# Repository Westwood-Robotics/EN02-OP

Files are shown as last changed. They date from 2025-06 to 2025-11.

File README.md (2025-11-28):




# EN02-OP

EN02-OP is the Open Source 3-Finger End-Effector created by Westwood Robotics and equiped on our full-size humanoid robot THEMIS. A very simple yet versital 7DoF design is adopter, enabling the end-effector to change into the best poses for all kinds of items. \
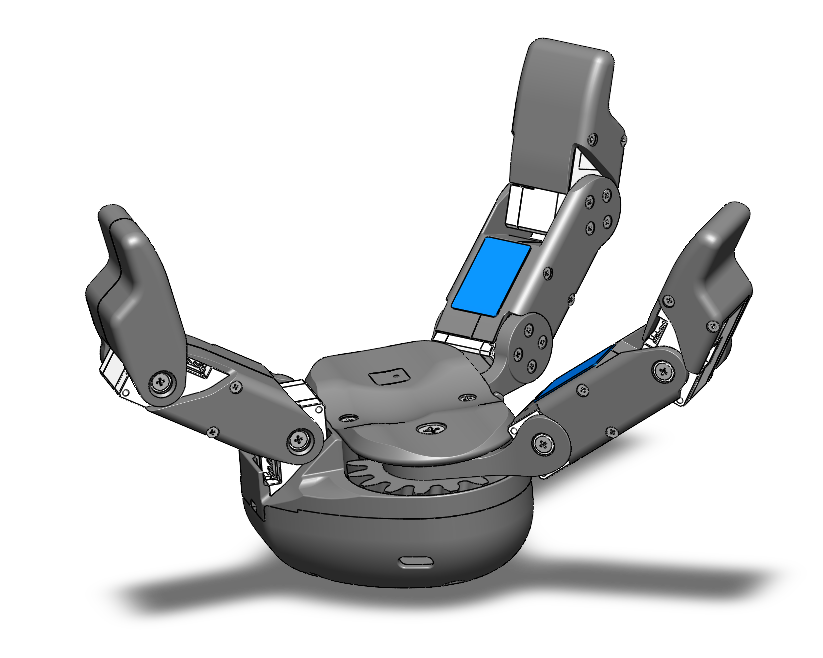
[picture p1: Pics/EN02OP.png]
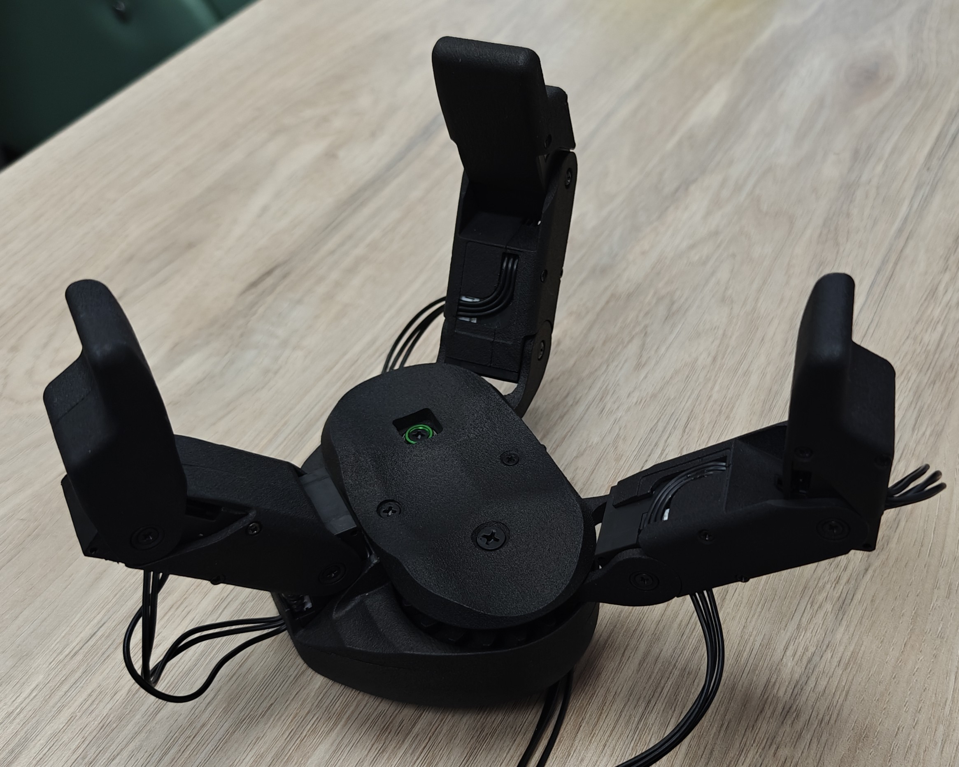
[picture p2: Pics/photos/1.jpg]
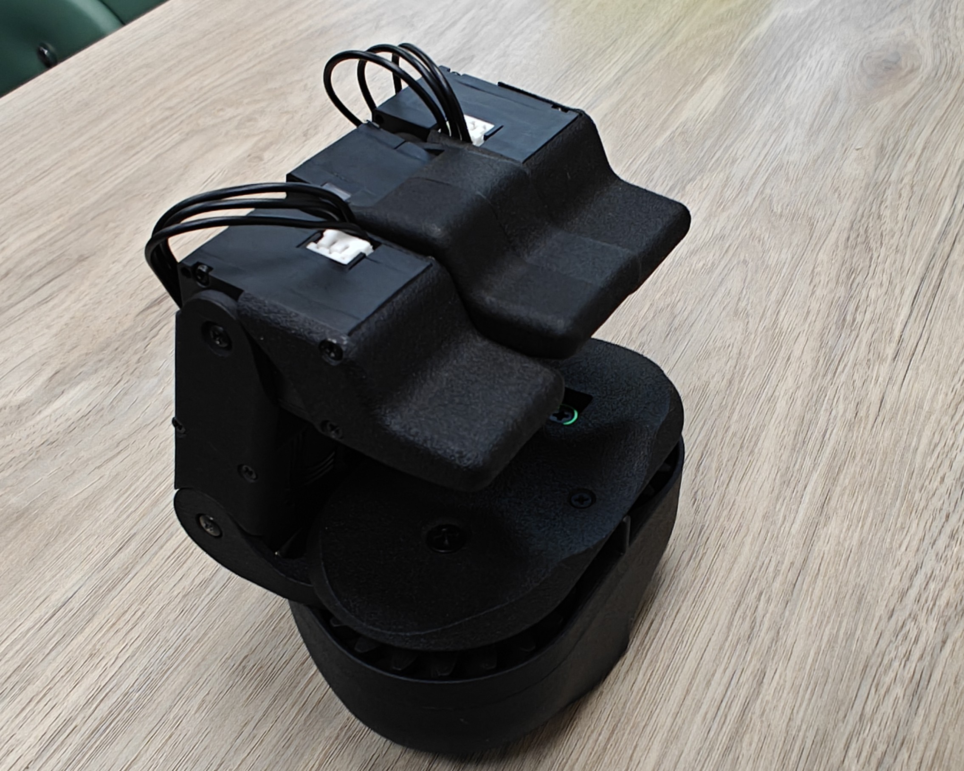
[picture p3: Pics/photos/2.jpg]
  \
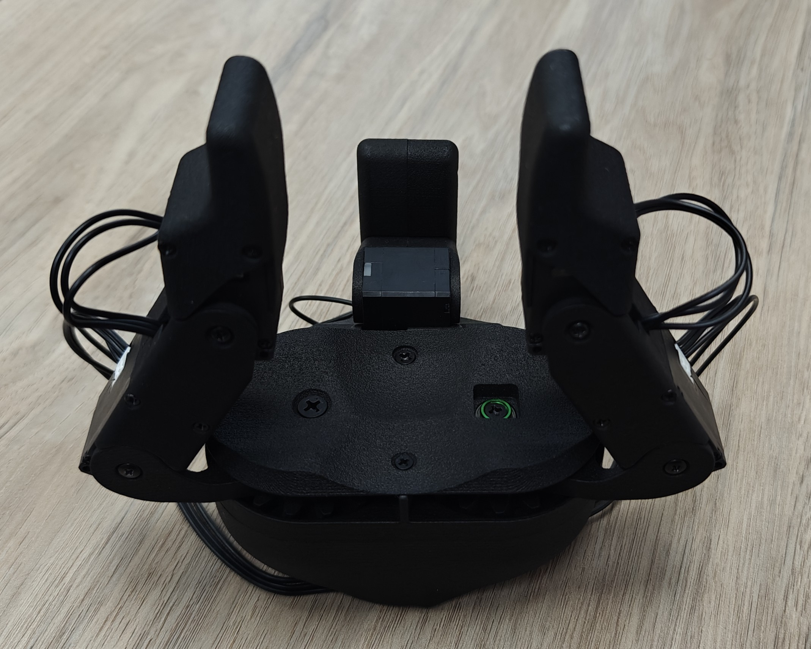
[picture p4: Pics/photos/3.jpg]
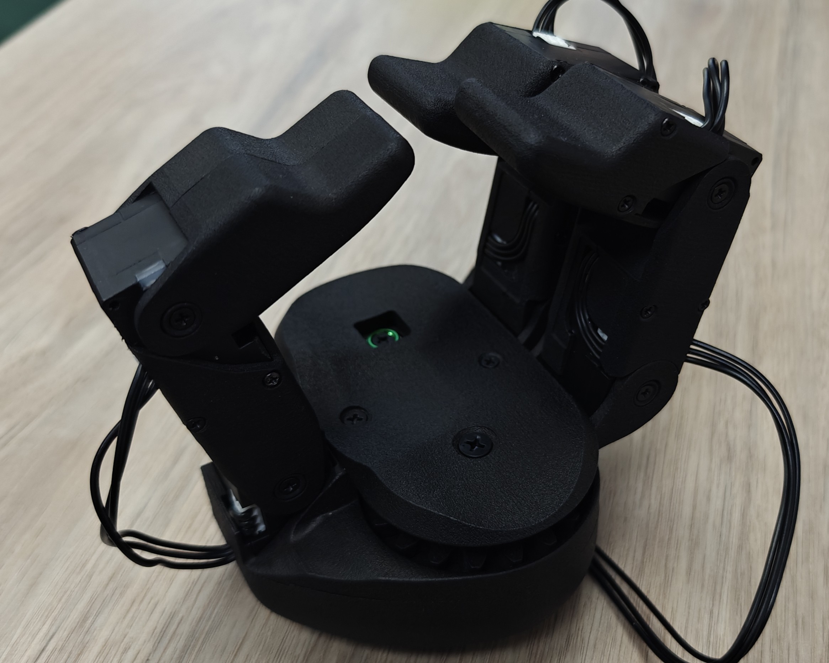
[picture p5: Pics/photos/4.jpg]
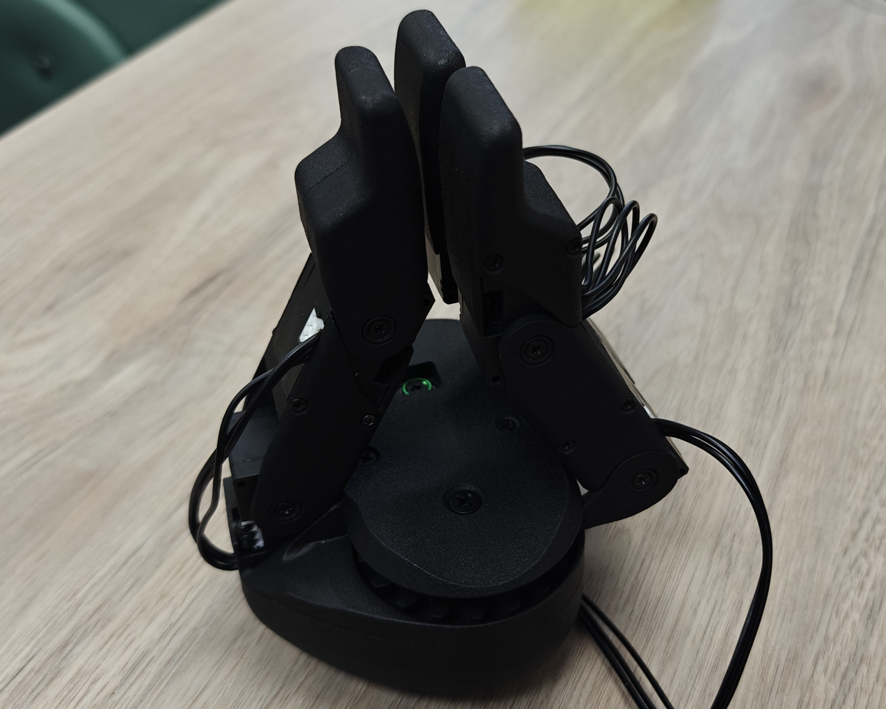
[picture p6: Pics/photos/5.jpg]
  \
Most parts on EN02-OP can be 3D printed, and all hadrware is standard and avalible off-the-shelf. The standard actuators on EN02-OP are the XC-330-M288-T($98.89/ea) from Dynamixel, but if the anticipated payload is realtively small, XL-330($26.29/ea) can be adopted for lower cost.

[Contact us](https://www.westwoodrobotics.io/contact/) to order an official version, or ***Build your EN02-OP for as low as $200!*** \
<sub> (Cost estimation based on using XL-330 for all 7DoF, parts printed with generic PLA material and Bambu PAHT-CF, and EN02OP-PWR PCBA assembled in-house. Tools and equipment not included.)  </sub>

## Build EN02-OP with Kevin!
Follow [this tutorial](https://www.youtube.com/watch?v=WY0bp_8Il1o) by [Kevin Wood](https://github.com/kevinwoodrobotics) to build your EN02-OP!

## Before You Start
### Know The Design
> [!IMPORTANT]
> Modify EN02-PALM_BASE to fit your system before printing.

> [!NOTE]
> Use fiber reinforced materials for parts in */Design/Parts_to_Print/CF_Reinforced/*

All design files of EN02-OP is included in [EN02-OP.STEP](/Design/EN02-OP.STEP). To make import easier, the 3D model of EN02OP-PWR(Board for voltage regulation and communication ports) is excluded from the model and provided seperatly in [EN02-PWR.step](/Design/EN02-PWR.step). Refer to [EN02-OP-BOM.xls](/Design/EN02-OP-BOM.xls) for the complete BOM of EN02-OP.

For your convenient, all parts that can be 3D printed are included in the [/Design/Parts_to_Print](/Design/Parts_to_Print/) folder. \
Feel free to go with your favorate materials for the parts in the [../Parts_to_Print/General](/Design/Parts_to_Print/General/) folder, such as PLA, PETG, ABS and Nylon, but it is highly recommended to print the parts in the [../Parts_to_Print/CF_Reinforced](/Design/Parts_to_Print/CF_Reinforced/) folder with carbon fiber/glass fiber reinforced materials for better strength and durability, such as Bambu PAHT-CF. The parts are highlighted in blue in the picture below:\
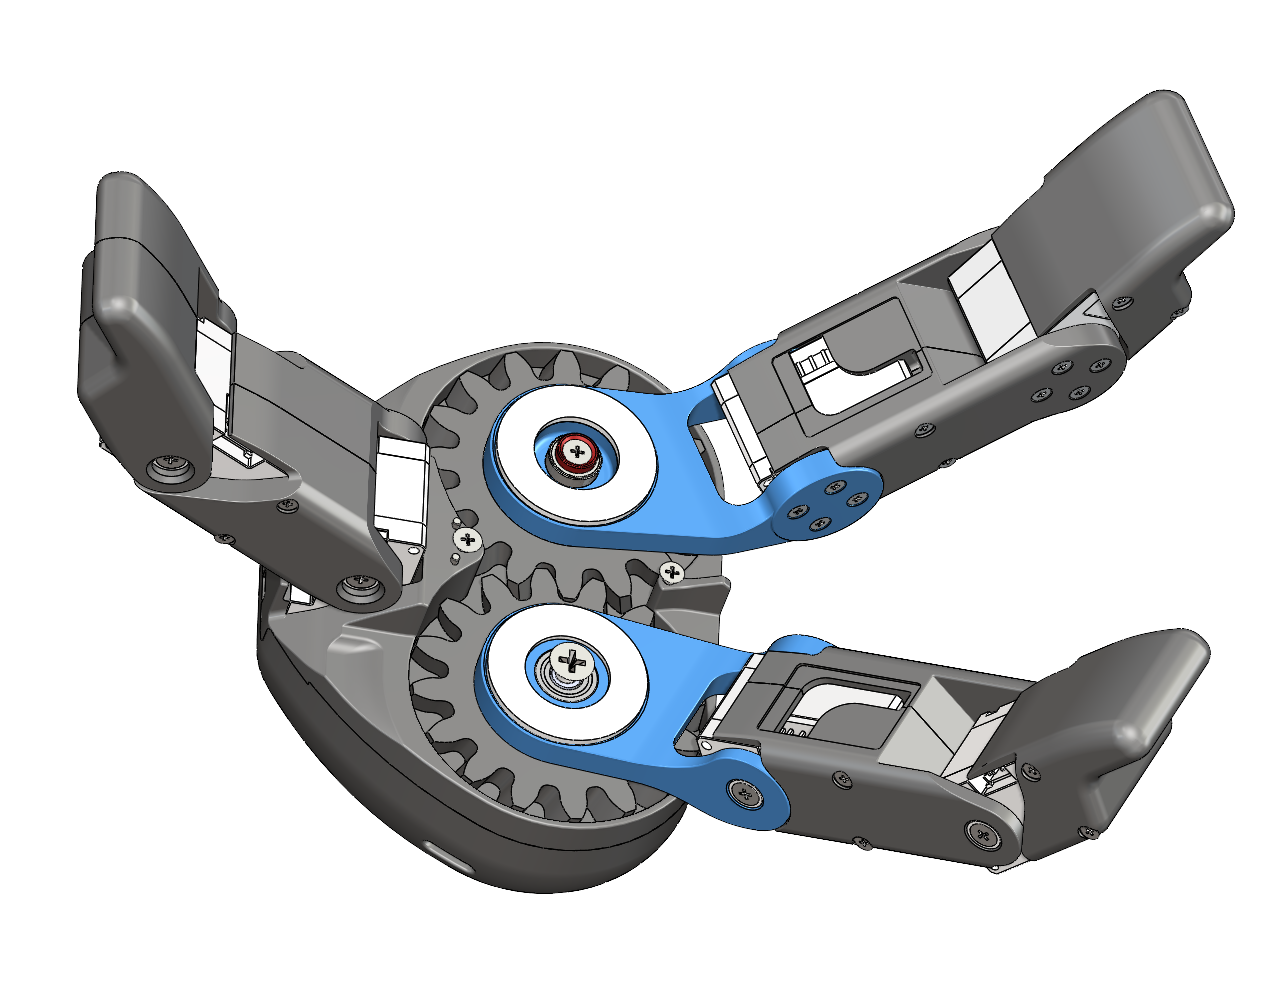
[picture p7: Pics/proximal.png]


**Modify [EN02-PALM_BASE](/Design/Parts_to_Print/General/Modify_Before_Printing/EN02-PALM_BASE.STEP) before printing!** \
EN02-OP is designed to be located and mounted onto robot manipulators using the plane with circular profile on the bottom, as highlighted in blue in the piture below. Mounting holes have been removed intentionally, so please modify the part and add mounting holes in a pattern that matches your robot manipulator before printing it.\
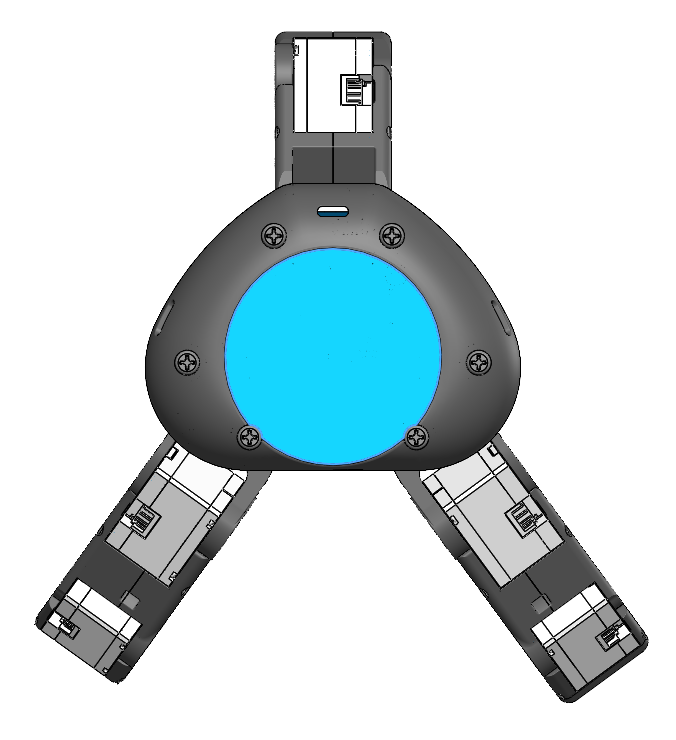
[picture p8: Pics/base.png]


### Electronics 
Electronics on EN02-OP is fairly simple and there is only one PCBA to fabracate which is the EN02-PWR. The XL/XC-330-M288-T actuators take 5V as input and their communication protocal is TTL. There is a 20~36V to 5V/10A regulator on EN02-PWR, making it compatible with the DC power supply on a large range of robot systems. It also takes care of chaining the fingers together. 

All related files are included in the [/Electronics](/Electronics) folder. Send [EN02OP-PWR-Gerber.zip](/Electronics/EN02OP-PWR-Gerber.zip) to your PCB manufacture to make the PCB board, and all components needed are listed in [EN02OP-PWR-BOM.xlsx](/Electronics/EN02OP-PWR-BOM.xlsx). Refer to [EN02OP-PWR.pdf](/Electronics/EN02OP-PWR.pdf) for the scheme of the board.

You can purchase pre-assembled EN02OP-PWR from us for $35/ea. Contact us at: https://www.westwoodrobotics.io/contact/

Each XL/XC-330 actuator comes with one pre-assembled cable. Cables with the same crimp and headers(JST EHR-03) in various length can also be found on Amazon and Ebay for affordable prices.
#### Can I modify EN02-PWR to support 12V systems?
Other models of XC330 actuators such as the T288 and the T181 models require 12V power supply, and EN02-PWR can be easily modified by relacing several components to support 12V. Please refer to tab "BOM_12V_EN02OP" in [EN02OP-PWR-BOM.xlsx](/Electronics/EN02OP-PWR-BOM.xlsx) for a full BOM for 12V output, and the items that are different from 5V setup has been highlighted.
> [!IMPORTANT]
> Make sure to always test the output of your EN02-PWR before using it. Avoid powering 5V actuators with 12V power supply.

> [!NOTE]
> The pre-assembled EN02OP-PWR from Westwood Robotics is 5V. You will need to modify the components according to BOM_12V_EN02OP by yourself if 12V is needed instead of 5V. Please note that any modification will void the board's warranty. 

## Assembly Notes
Please refer to [EN02 Assembly Guide.pdf](/EN02_Assembly_Guide.pdf) for detailed assemble instructions. Feel free to contact us should you encounter any challenge.

## Control Software
There is no dedicated control software for EN02-OP at the moment. It is realatively easy to work with given its simple structure, and please refer to https://emanual.robotis.com/docs/en/dxl/x/xc330-m288/ for more information on how to work with Dynamixel actuators.

## Licensing
The work in this repo is under GNU General Public License (GPL) version 3, which is ideal for use cases such as open-source projects with open-source distribution, student/academic purposes, hobby projects, internal research projects without external distribution, or other projects where all GPL obligations can be met. Read the full text of [the GNU GPL version 3](https://www.gnu.org/licenses/gpl-3.0.html) for details.  

Contact us for commercial license should you need full rights to create and distribute the platform on your own terms without any open-source license obligations.

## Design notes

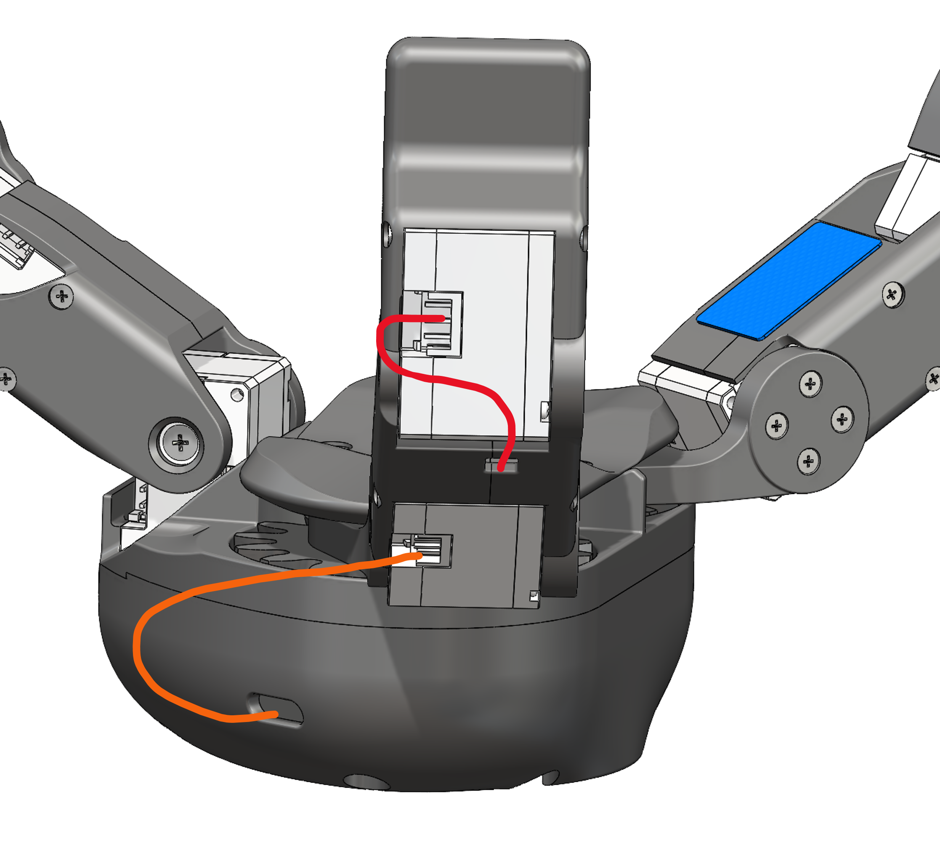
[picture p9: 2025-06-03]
Pics/wire2.png

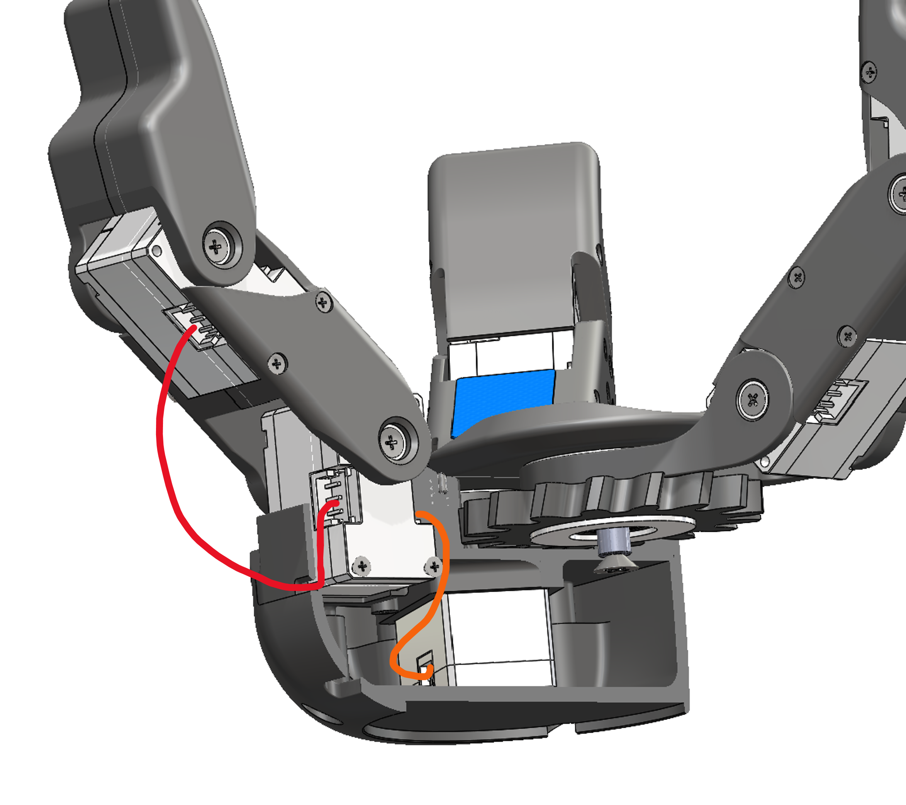
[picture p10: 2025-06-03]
Pics/wire3.png

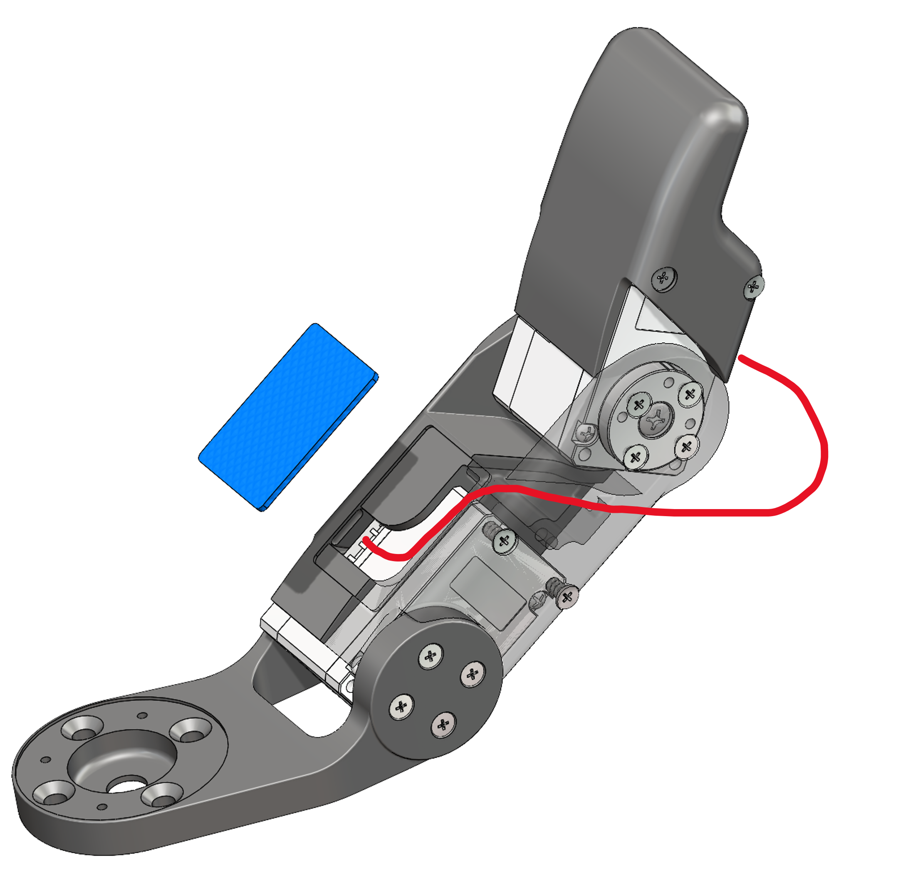
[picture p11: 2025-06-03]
Pics/wire1.png

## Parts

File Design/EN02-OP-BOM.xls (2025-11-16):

Item | Part# | Name | Description | QTY | Note
1 | EN02-01-01-01 | EN02-PALM_TOP |  | 1 | Print with PLA/ABS/Nylon/PETG
2 | EN02-01-01-02 | EN02-PALM_TOP_CAP |  | 1 | Print with PLA/ABS/Nylon/PETG
3 | EN02-01-01-03 | EN02-PALM_MIDHOUSING |  | 1 | Print with PLA/ABS/Nylon/PETG
4 | EN02-01-01-04 | EN02-PALM_BASE |  | 1 | MODIFY BEFORE PRINTING; Print with PLA/ABS/Nylon/PETG
5 | EN02-01-02-01 | EN02-MASTER_GEAR | M3_T16_H6_15deg_DC_-1.0 | 1 | Print with PLA/ABS/Nylon/PETG
6 | EN02-01-02-02 | EN02-SLAVE_GEAR | M3_T16_H6_15deg_DC_-1.0_SLAVE | 1 | Print with PLA/ABS/Nylon/PETG
7 | EN02-01-02-03 | EN02-SLAVE_SHAFT |  | 1 | Print with PLA/ABS/Nylon/PETG
8 | EN02-01-03-01 | EN02-PWR | EN02-POWER_BOARD, 5V OUTPUT, 20-36V INPUT | 1 | Solder power cable before assembly
9 | EN02-01-03-02 | EN02-DXL_CABLE_S | EHR cable for Dynamixel Actuators, 15~16cm | 3
10 | EN02-01-03-03 | EN02-DXL_CABLE_L | EHR cable for Dynamixel Actuators, 19~20cm | 3
11 | EN02-01-03-04 | EN02-DXL_CABLE_J | EHR cable for Dynamixel Actuators, 5~6cm | 1
12 | EN02-02-01-01 | EN02-PROXIMAL_PHALANX |  | 1 | Print with CF reinforced materials
13 | EN02-02-02-01 | EN02-MIDDLE_PHALANX |  | 1 | Print with PLA/ABS/Nylon/PETG
14 | EN02-02-03-01 | EN02-DISTAL_PHALANX |  | 1 | Print with PLA/ABS/Nylon/PETG
15 | EN02-03-01-01 | EN02-PROXIMAL_PHALANX-M |  | 1 | Print with CF reinforced materials
16 | EN02-03-02-01 | EN02-MIDDLE_PHALANX_M |  | 1 | Print with PLA/ABS/Nylon/PETG
17 | EN02-03-03-01 | EN02-DISTAL_PHALANX-M |  | 1 | Print with PLA/ABS/Nylon/PETG
18 | EN02-04-01-01 | EN02-THUMB_MIDDLE_PHALANX |  | 1 | Print with PLA/ABS/Nylon/PETG
19 | EN02-04-02-01 | EN02-THUMB_DISTAL_PHALANX |  | 1 | Print with PLA/ABS/Nylon/PETG
20 | XL-XC-330 | DYNAMIXEL XC/XL330-M288-T | DYNAMIXEL SERVO ACTUATOR | 7
21 | IDLER-XL-XC-330 | IDLER | IDLER FOR 330 ACTUATOR | 7 | Print with PLA/ABS/Nylon/PETG
22 | JTM-1630-015 | THRUST_BEARING_16x30x1.5 | IGUS Thrust Washer | 3
23 | 106ZZ | 106ZZ | Precision Stainless Steel Ball Bearing | 1
24 | 126ZZ | 126ZZ | Stainless Steel Ball Bearing | 2
25 | WASHER_M3_FLATHEAD | METAL WASHER FOR FLATHEAD SCREW, M3 | METAL WASHER FOR FLATHEAD SCREW, M3 | 1
26 | TRS-M3x8_FLAT | TRS-M3x8_FLAT | Stainless Steel Flat Head Thread-Forming Screws for Plastic | 7
27 | TRS-M2.2x12_FLAT | TRS-M2.2x12_FLAT | Stainless Steel Flat Head Thread-Forming Screws for Plastic | 28
28 | TRS-M2x5_FLAT_PHILLIPS | TRS-M2x5_FLAT_PHILLIPS | Stainless Steel Flat Head Thread-Forming Screws for Plastic | 24
29 | TRS-M2.5x24_FLAT_PHILLIPS | TRS-M2.5x24_FLAT_PHILLIPS | Stainless Steel Flat Head Thread-Forming Screws for Plastic | 2
30 | TRS-M3x12_FLAT | TRS-M3x12_FLAT | Stainless Steel Flat Head Thread-Forming Screws for Plastic | 1
31 | TRS-M3x10_FLAT | TRS-M3x10_FLAT | Stainless Steel Flat Head Thread-Forming Screws for Plastic | 8
32 | TRS-M2x8_FLAT_PHILLIPS | TRS-M2x8_FLAT_PHILLIPS | Stainless Steel Flat Head Thread-Forming Screws for Plastic | 4
33 | TRS-M2.5x8_FLAT | TRS-M2.5x8_FLAT | Stainless Steel Flat Head Thread-Forming Screws for Plastic | 1
34 | TRS-M4x10_ROUND | TRS-M4x10_ROUND | Phillips Rounded Head Thread-Forming Screws | 6
35 | TRS-M4x12_FLAT | TRS-M4x12_FLAT | Stainless Steel Flat Head Thread-Forming Screws for Plastic | 2
36 | TRS-M2.5x6_ROUND | TRS-M2.5x6_ROUND | Phillips Rounded Head Thread-Forming Screws | 1
37 | D1.5x5 | DOWEL PIN, DIAMETER 1.5MM, LENGTH 5MM | 18-8 Stainless Steel Dowel Pin | 2
38 | D1.5x10 | DOWEL PIN, DIAMETER 1.5MM, LENGTH 10MM | 18-8 Stainless Steel Dowel Pin | 6
39 | D2x5 | DOWEL PIN, DIAMETER 2MM, LENGTH 5MM | 18-8 Stainless Steel Dowel Pin | 5
40 | SW-4 | Spiral Wrap, ID 4mm

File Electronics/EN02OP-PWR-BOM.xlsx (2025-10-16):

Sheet: BOM_5V_EN02OP
No. | Quantity | Designator | Footprint | Value | Comment | Description
1 | 2 | C11,C12 | C1210 | 4.7uF | 4.7uF | Capacitance:4.7uF;Tolerance:±10%;Rated Voltage:100V;Capacitance:Temperature Coefficient:X7S;
2 | 1 | C13 | C0805 | 470nF | 470nF | Capacitance:470nF;Tolerance:±10%;Rated Voltage:100V;Capacitance:Temperature Coefficient:X7R;
3 | 1 | C15 | C0603 | 1uF | 1uF | Capacitance:1uF;Tolerance:±10%;Rated Voltage:16V;Capacitance:Temperature Coefficient:X7R;
4 | 1 | C16 | C0805 | 4.7uF | 4.7uF | Capacitance:4.7uF;Tolerance:±10%;Rated Voltage:16V;Capacitance:Temperature Coefficient:X7R;
5 | 1 | C18 | C0603 | 680pF | 680pF | Capacitance:680pF;Tolerance:±10%;Rated Voltage:50V;Capacitance:Temperature Coefficient:X7R;
6 | 1 | C20 | C0603 | 10nF | 10nF | Capacitance:10nF;Tolerance:±10%;Rated Voltage:50V;Capacitance:Temperature Coefficient:X7R;
7 | 1 | C21 | C0603 | 100nF | 100nF | Capacitance:100nF;Tolerance:±10%;Rated Voltage:16V;Capacitance:Temperature Coefficient:X7R;
8 | 1 | C23 | C1210 | 22uF | 22uF | Capacitance:22uF;Tolerance:±10%;Rated Voltage:16V;Capacitance:Temperature Coefficient:X7R;
9 | 1 | C24 | C0603 | 220pF | 220pF | Capacitance:220pF;Tolerance:±10%;Rated Voltage:100V;Capacitance:Temperature Coefficient:X7R;
10 | 1 | C26 | CAP-SMD_L7.3-W4.3-L-FD | 220uF | Tantalum Capacitors | Capacitance:220uF;Tolerance:±20%;Rated Voltage:16V
11 | 1 | C27 | C0603 | NS | NS
12 | 1 | C28 | C0603 | NS | NS
13 | 1 | CN1 | CONN-SMD_4P-P1.25-Horizontal
14 | 1 | D1 | SOD-323_L1.8-W1.3-LS2.5-RD |  | 1N4148WS | Switching Diodes, 1N4148WS
15 | 1 | D2 | POWERDI-123_L2.8-W1.8-LS3.7-RD |  | DFLS1150-7 | Schottky Diodes 150V 1A
16 | 3 | INDEX_L,INDEX_R,THUMB | CONN-TH_3P-P2.50-Horizontal |  | S3B-EH(LF)(SN)
17 | 1 | L2 | IND-SMD_L13.45-W12.6 | 4.7uH | 4.7uH | 4.7uH;Tolerance:±20%;Rated Current:15A;
18 | 2 | Q3,Q4 | DFN-8_L3.0-W3.0-P0.65-BL-EP_PE5G6EA |  | WSD4038DN33 | 40V 38A 2.1W 13mΩ@10V,7A 2.5V 1 N-channel DFN-8(3x3) MOSFETs
19 | 2 | R10,R16 | R0603 | 37.4kΩ | 37.4kΩ | Resistance:37.4kΩ;Tolerance:±1%;Power:100mW;Temperature Coefficient:±100ppm/℃;SMD
20 | 2 | R11,R13 | R0603 | 100kΩ | 100kΩ | Resistance:100kΩ;Tolerance:1%;Power:100mW;
21 | 5 | R12,R19,R21,R24,R25 | R0603 | 0Ω | 0Ω | Resistance:0Ω;Tolerance:±5%;Power:100mW;Temperature Coefficient:±800ppm/℃;SMD
22 | 1 | R14 | R0603 | 1MΩ | 1MΩ | Resistance:1MΩ;Tolerance:±1%;Power:100mW;Temperature Coefficient:±100ppm/℃;SMD
23 | 1 | R17 | R0603 | 51kΩ | 51kΩ | Thick Film Resistors
24 | 2 | R18,R30 | R0603 | NS | NS
25 | 1 | R20 | R0603 | 2.2Ω | 2.2Ω | Resistance:2.2Ω;Tolerance:±1%;Power:100mW;Temperature Coefficient:±400ppm/℃;SMD
26 | 2 | R22,R29 | R0603 | 10 | 10 | Resistance:10Ω;Tolerance:±1%;Power:100mW;Temperature Coefficient:±400ppm/℃;SMD
27 | 1 | R23 | RES-SMD_L6.4-W3.2-1 | 7mΩ | 7mΩ | Resistance:7mΩ;Tolerance:±1%;Power:2W;Temperature Coefficient:±100ppm/℃;
28 | 1 | R26 | R0603 | 63.4K | 63.4K | Thick Film Resistors
29 | 1 | R27 | R0603 | 12kΩ | 12kΩ | Resistance:12kΩ;Tolerance:±1%;Power:100mW;Temperature Coefficient:±100ppm/℃;SMD
30 | 1 | U5 | TSSOP-20-EP |  | MP9928GF | 4V-60V INPUT, CURRENT MODE, SYNC
31 | 1 | U13 | CAP-SMD_BD6.3-L6.6-W6.6-FD | 47uF | 47uF | 47uF 50V 195mA@100kHz 680mΩ@100kHz ±20% SMD,D6.3xL5.8mm Aluminum Electrolytic Capacitors

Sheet: BOM_12V_EN02OP
No. | Quantity | Designator | Footprint | Value | Comment | Description
1 | 2 | C11,C12 | C1210 | 4.7uF | 4.7uF | Capacitance:4.7uF;Tolerance:±10%;Rated Voltage:100V;Capacitance:Temperature Coefficient:X7S;
2 | 1 | C13 | C0805 | 470nF | 470nF | Capacitance:470nF;Tolerance:±10%;Rated Voltage:100V;Capacitance:Temperature Coefficient:X7R;
3 | 1 | C15 | C0603 | 1uF | 1uF | Capacitance:1uF;Tolerance:±10%;Rated Voltage:16V;Capacitance:Temperature Coefficient:X7R;
4 | 1 | C16 | C0805 | 4.7uF | 4.7uF | Capacitance:4.7uF;Tolerance:±10%;Rated Voltage:16V;Capacitance:Temperature Coefficient:X7R;
5 | 1 | C18 | C0603 | 220pF | 220pF | Capacitance:220pF;Tolerance:±10%;Rated Voltage:50V;Capacitance:Temperature Coefficient:X7R;
6 | 1 | C20 | C0603 | 10nF | 10nF | Capacitance:10nF;Tolerance:±10%;Rated Voltage:50V;Capacitance:Temperature Coefficient:X7R;
7 | 1 | C21 | C0603 | 100nF | 100nF | Capacitance:100nF;Tolerance:±10%;Rated Voltage:16V;Capacitance:Temperature Coefficient:X7R;
8 | 1 | C23 | C1210 | 22uF | 22uF | Capacitance:22uF;Tolerance:±10%;Rated Voltage:16V;Capacitance:Temperature Coefficient:X7R;
9 | 1 | C24 | C0603 | 220pF | 220pF | Capacitance:220pF;Tolerance:±10%;Rated Voltage:100V;Capacitance:Temperature Coefficient:X7R;
10 | 1 | C26 | CAP-SMD_L7.3-W4.3-L-FD | 220uF | Tantalum Capacitors | Capacitance:220uF;Tolerance:±20%;Rated Voltage:16V
11 | 1 | C27 | C0603 | 82pF | 82pF | Capacitance:82pF;Tolerance:±10%;Rated Voltage:50V;Capacitance:Temperature Coefficient:X7R;
12 | 1 | C28 | C0603 | 150pF | 150pF | Capacitance:150pF;Tolerance:±10%;Rated Voltage:50V;Capacitance:Temperature Coefficient:X7R;
13 | 1 | CN1 | CONN-SMD_4P-P1.25-Horizontal
14 | 1 | D1 | SOD-323_L1.8-W1.3-LS2.5-RD |  | 1N4148WS | Switching Diodes, 1N4148WS
15 | 1 | D2 | POWERDI-123_L2.8-W1.8-LS3.7-RD |  | DFLS1150-7 | Schottky Diodes 150V 1A
16 | 3 | INDEX_L,INDEX_R,THUMB | CONN-TH_3P-P2.50-Horizontal |  | S3B-EH(LF)(SN)
17 | 1 | L2 | IND-SMD_L13.45-W12.6 | 4.7uH | 4.7uH | 4.7uH;Tolerance:±20%;Rated Current:15A;
18 | 2 | Q3,Q4 | DFN-8_L3.0-W3.0-P0.65-BL-EP_PE5G6EA |  | WSD4038DN33 | 40V 38A 2.1W 13mΩ@10V,7A 2.5V 1 N-channel DFN-8(3x3) MOSFETs
19 | 2 | R10,R16 | R0603 | 37.4kΩ | 37.4kΩ | Resistance:37.4kΩ;Tolerance:±1%;Power:100mW;Temperature Coefficient:±100ppm/℃;SMD
20 | 2 | R11,R13 | R0603 | 100kΩ | 100kΩ | Resistance:100kΩ;Tolerance:1%;Power:100mW;
21 | 5 | R12,R19,R21,R24,R25 | R0603 | 0Ω | 0Ω | Resistance:0Ω;Tolerance:±5%;Power:100mW;Temperature Coefficient:±800ppm/℃;SMD
22 | 1 | R14 | R0603 | 1MΩ | 1MΩ | Resistance:1MΩ;Tolerance:±1%;Power:100mW;Temperature Coefficient:±100ppm/℃;SMD
23 | 1 | R17 | R0603 | 10kΩ | 10kΩ | Thick Film Resistors
24 | 2 | R18 | R0603 | NS | NS
25 | 1 | R20 | R0603 | 2.2Ω | 2.2Ω | Resistance:2.2Ω;Tolerance:±1%;Power:100mW;Temperature Coefficient:±400ppm/℃;SMD
26 | 2 | R22 | R0603 | 2.2Ω | 2.2Ω | Resistance:2.2Ω;Tolerance:±1%;Power:100mW;Temperature Coefficient:±400ppm/℃;SMD
27 | 2 | R29 | R0603 | 10 | 10 | Resistance:10Ω;Tolerance:±1%;Power:100mW;Temperature Coefficient:±400ppm/℃;SMD
28 | 1 | R23 | RES-SMD_L6.4-W3.2-1 | 7mΩ | 7mΩ | Resistance:7mΩ;Tolerance:±1%;Power:2W;Temperature Coefficient:±100ppm/℃;
29 | 1 | R26 | R0603 | 169kΩ | 169kΩ | Thick Film Resistors
30 | 1 | R27 | R0603 | 12kΩ | 12kΩ | Resistance:12kΩ;Tolerance:±1%;Power:100mW;Temperature Coefficient:±100ppm/℃;SMD
31 | 1 | U5 | TSSOP-20-EP |  | MP9928GF | 4V-60V INPUT, CURRENT MODE, SYNC
32 | 1 | U13 | CAP-SMD_BD6.3-L6.6-W6.6-FD | 47uF | 47uF | 47uF 50V 195mA@100kHz 680mΩ@100kHz ±20% SMD,D6.3xL5.8mm Aluminum Electrolytic Capacitors
33 | 1 | R30 | R0603 | 0Ω | 0Ω | Resistance:0Ω;Tolerance:±5%;Power:100mW;Temperature Coefficient:±800ppm/℃;SMD

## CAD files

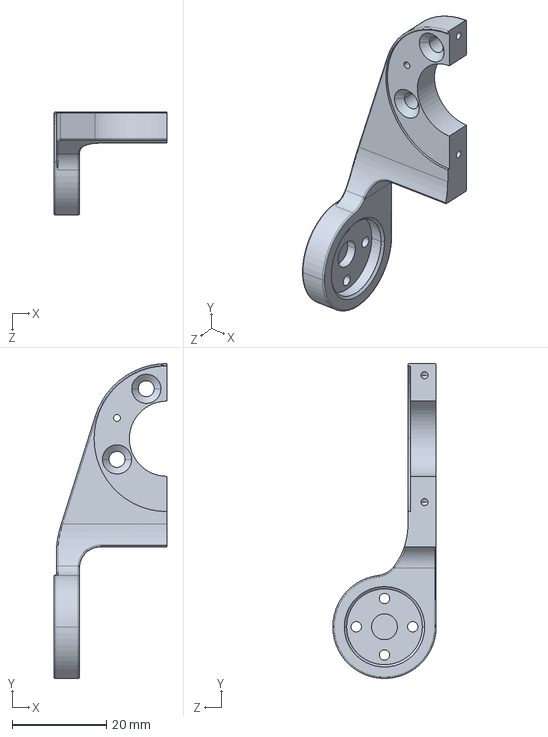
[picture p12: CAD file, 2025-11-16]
Design/Parts_to_Print/CF_Reinforced/EN02-PROXIMAL_PHALANX-1.STEP
24.0 x 67.0 x 22.0 mm

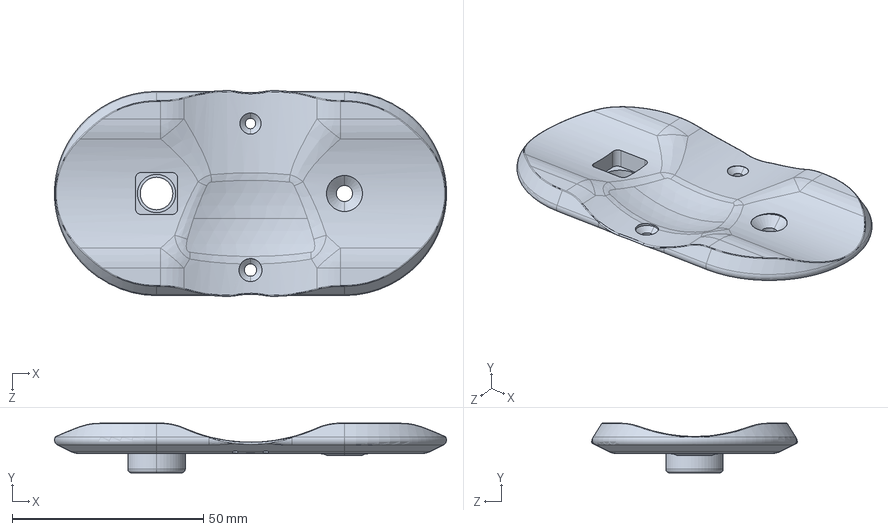
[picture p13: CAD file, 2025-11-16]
Design/Parts_to_Print/General/EN02-PALM_TOP.STEP
102.4 x 13.0 x 53.7 mm

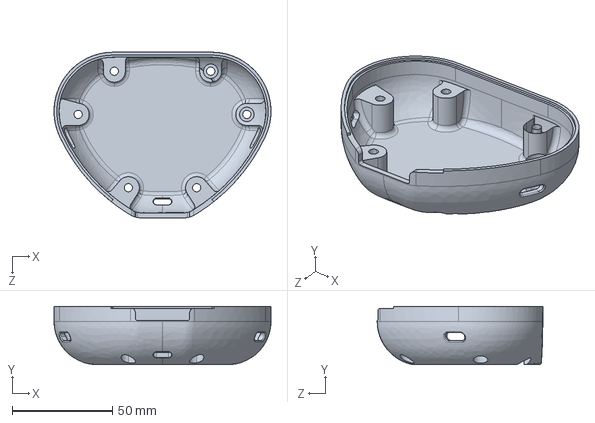
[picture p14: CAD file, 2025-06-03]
Design/Parts_to_Print/General/Modify_Before_Printing/EN02-PALM_BASE.STEP
108.1 x 29.0 x 82.5 mm

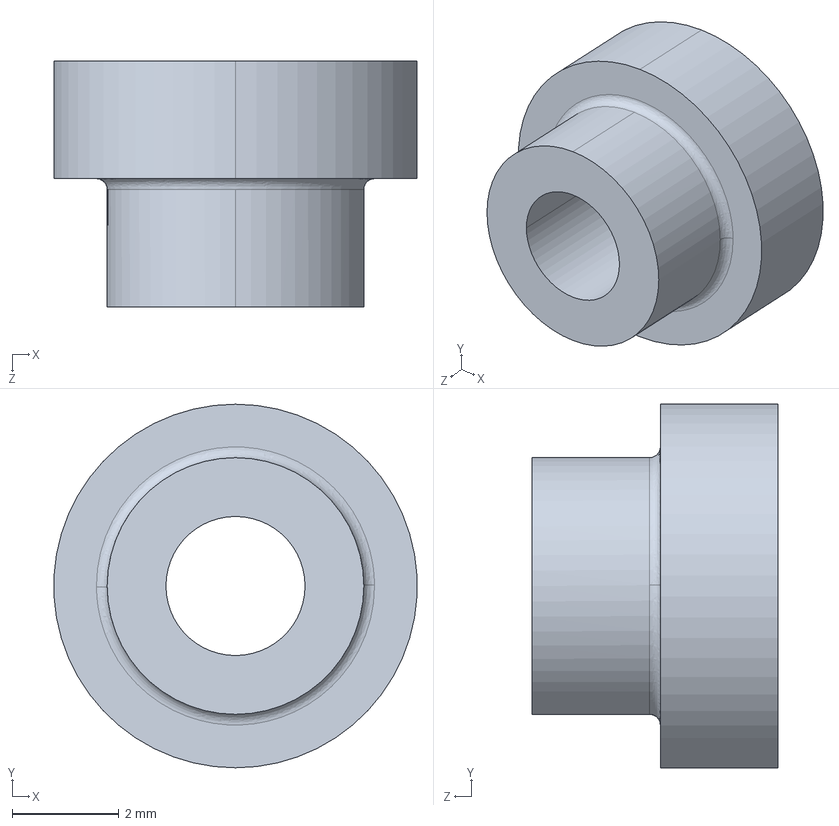
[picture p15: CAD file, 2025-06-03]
Design/Parts_to_Print/General/Print_6_of_these/IDLER-XL-XC-330.STEP
6.79 x 6.80 x 4.60 mm

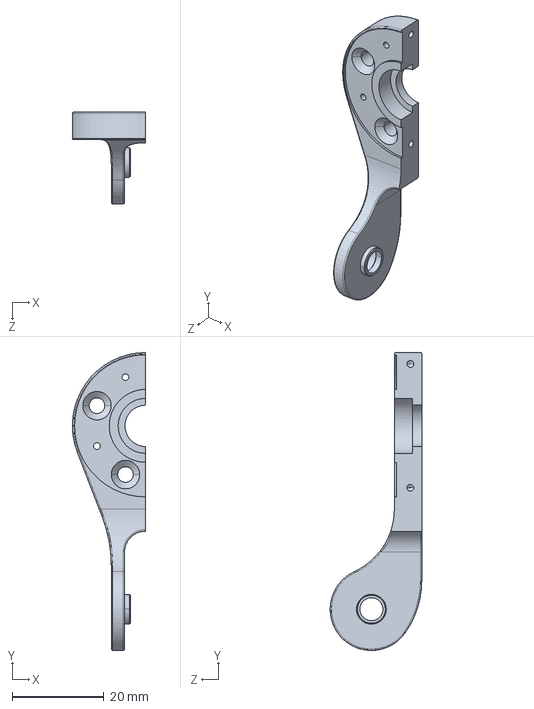
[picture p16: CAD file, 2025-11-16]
Design/Parts_to_Print/CF_Reinforced/EN02-PROXIMAL_PHALANX-M-1.STEP
16.0 x 65.0 x 20.0 mm

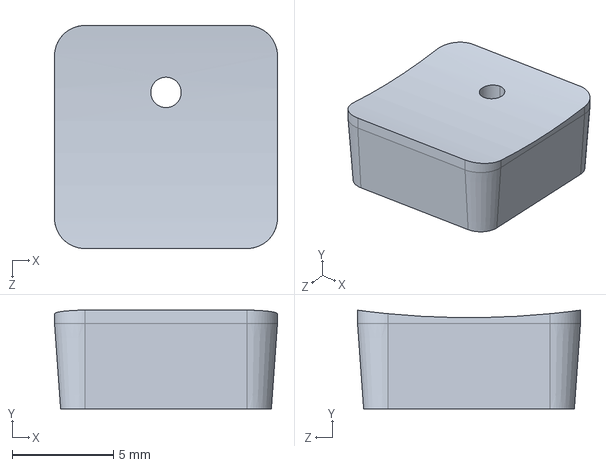
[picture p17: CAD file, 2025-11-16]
Design/Parts_to_Print/General/EN02-PALM_TOP_CAP.STEP
11.0 x 4.87 x 11.0 mm

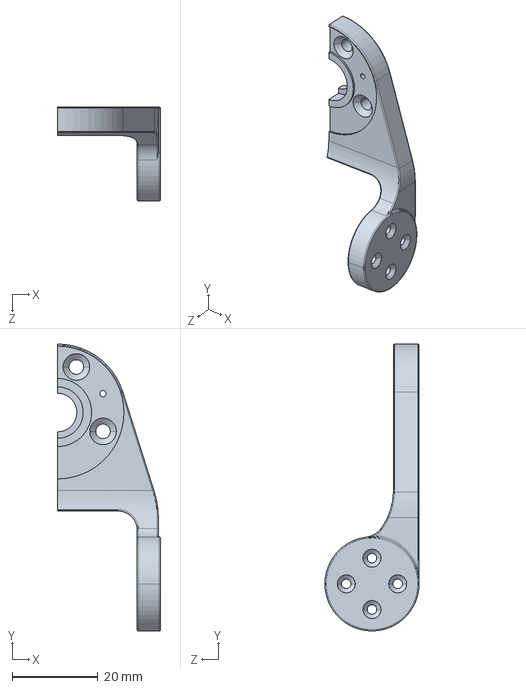
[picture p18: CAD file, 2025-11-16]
Design/Parts_to_Print/CF_Reinforced/EN02-PROXIMAL_PHALANX-M-2.STEP
24.0 x 67.0 x 22.0 mm

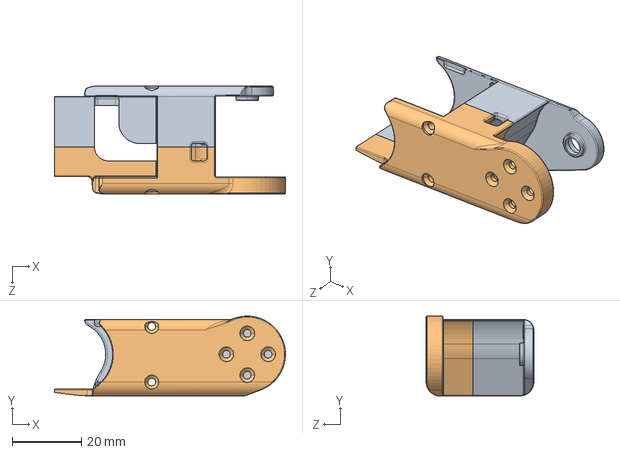
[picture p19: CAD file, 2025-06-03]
Design/Parts_to_Print/General/EN02-MIDDLE_PHALANX_M.STEP
66.5 x 23.0 x 31.0 mm

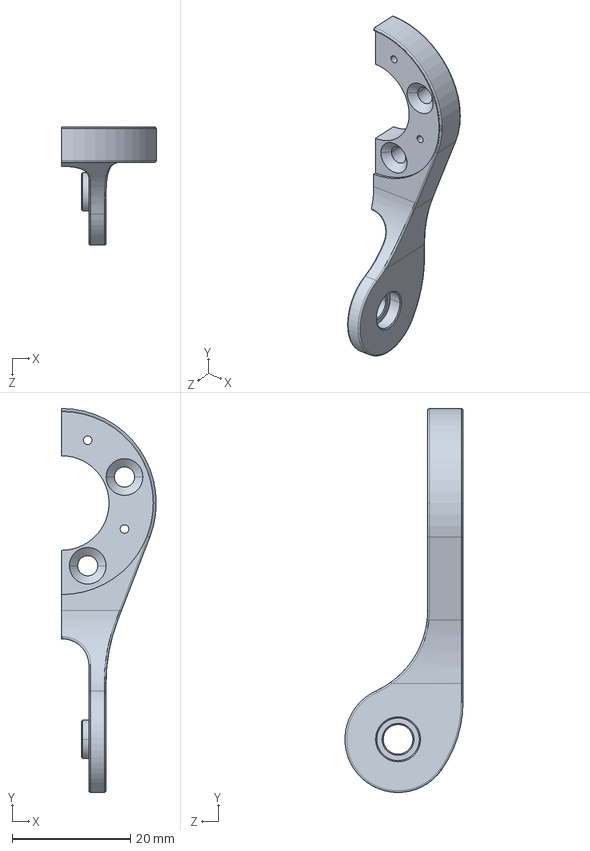
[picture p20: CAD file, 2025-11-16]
Design/Parts_to_Print/CF_Reinforced/EN02-PROXIMAL_PHALANX-2.STEP
16.0 x 65.0 x 20.0 mm

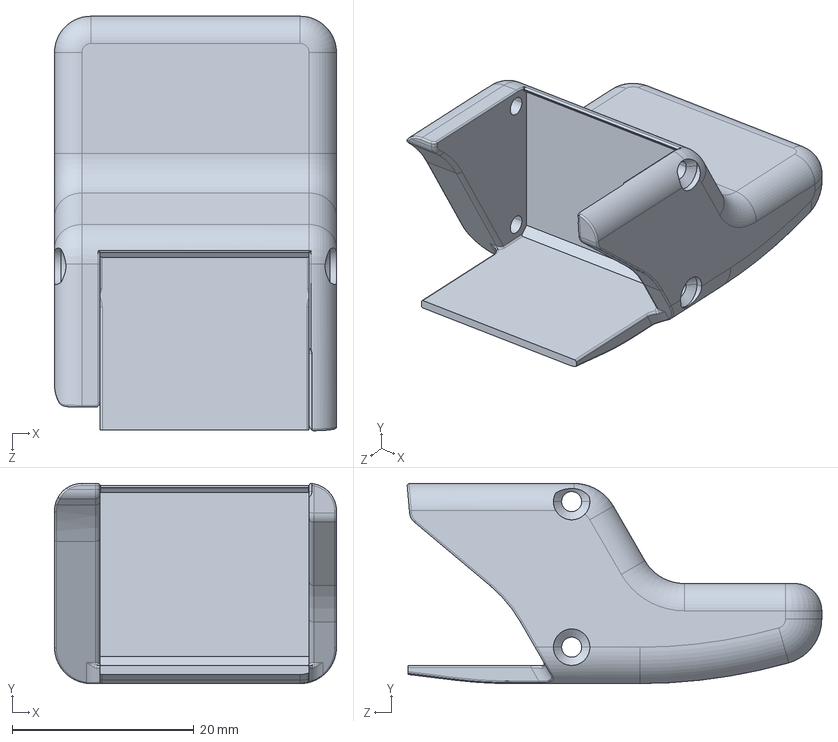
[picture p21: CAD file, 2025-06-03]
Design/Parts_to_Print/General/EN02-DISTAL_PHALANX.STEP
31.0 x 22.0 x 45.6 mm

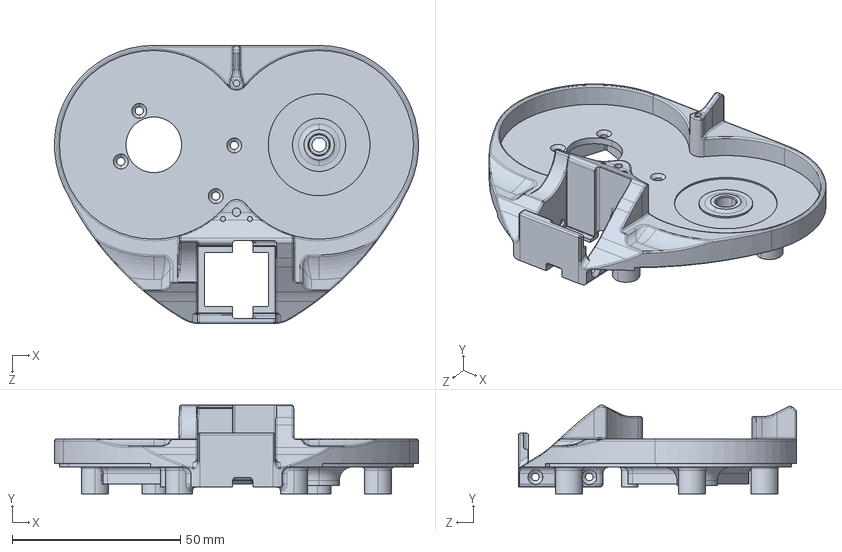
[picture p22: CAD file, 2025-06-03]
Design/Parts_to_Print/General/EN02-PALM_MIDHOUSING.STEP
108.0 x 26.4 x 82.6 mm

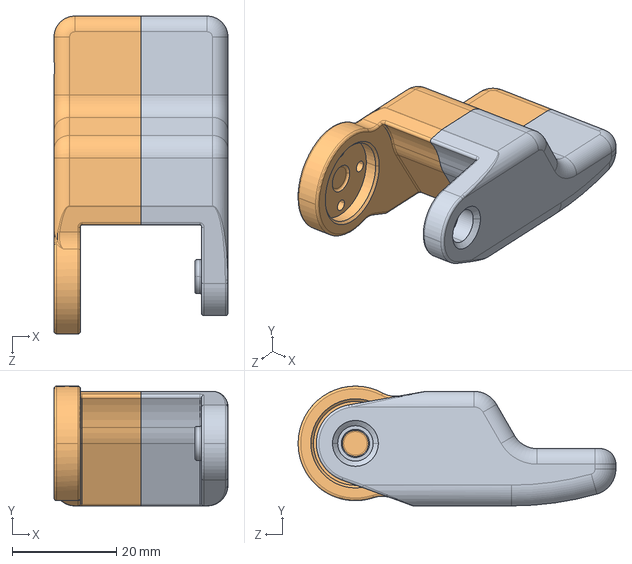
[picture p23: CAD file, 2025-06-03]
Design/Parts_to_Print/General/EN02-THUMB_DISTAL_PHALANX.STEP
33.4 x 23.0 x 61.0 mm

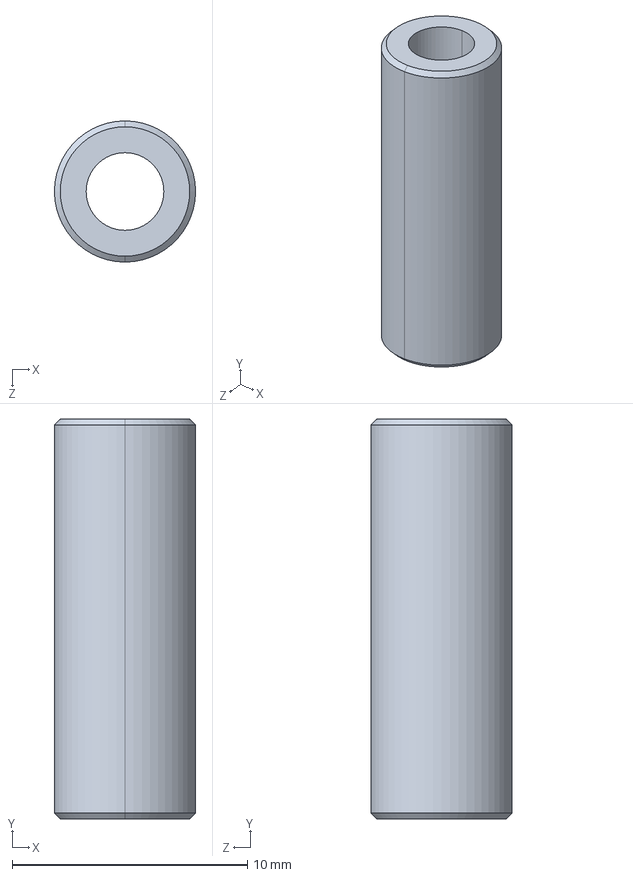
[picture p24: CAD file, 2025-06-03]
Design/Parts_to_Print/General/SLAVE_SHAFT.STEP
6.00 x 17.0 x 6.00 mm

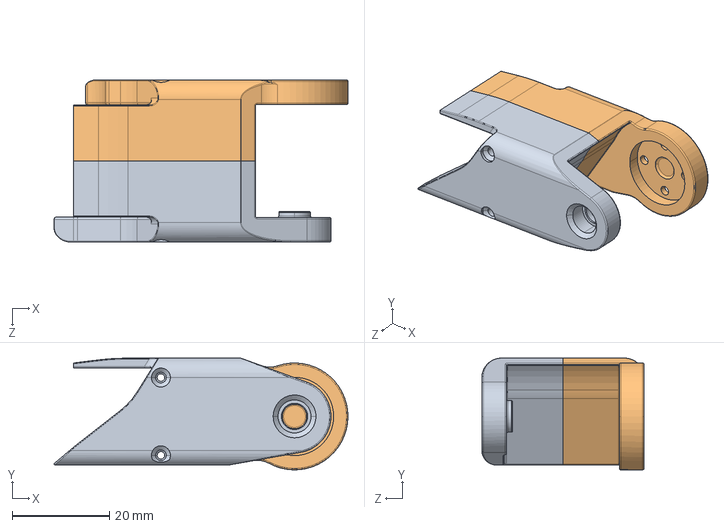
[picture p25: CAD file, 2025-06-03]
Design/Parts_to_Print/General/EN02-THUMB_MIDDLE_PHALANX.STEP
60.5 x 23.0 x 33.4 mm

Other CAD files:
Design/Parts_to_Print/General/EN02-DISTAL_PHALANX-M.STEP
Design/Parts_to_Print/General/EN02-MIDDLE_PHALANX.STEP

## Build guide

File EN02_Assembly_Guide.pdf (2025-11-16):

# EN02-OP

## Open-Source Robot End-Effector

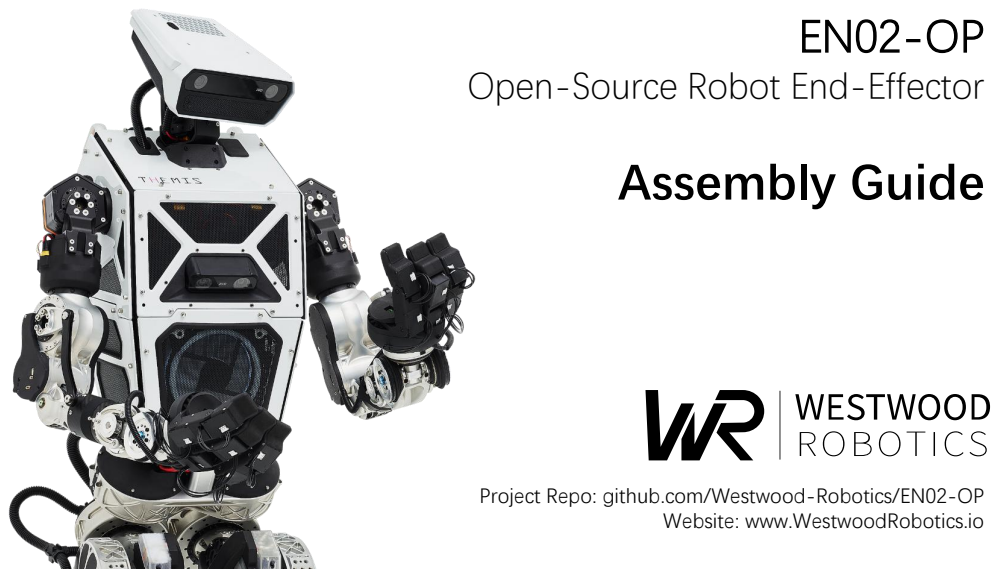
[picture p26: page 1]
Assembly Guide

Project Repo: github.com/Westwood-Robotics/EN02-OP

Website: www.WestwoodRobotics.io

### EN02 BOM Preparation:

S1 | S6 S5 S3 | S4

S7

S2

S8
S9

S10

S11

B1 B2

B3

B4

P1

P2

P3

PALM_TOP

PALM_
MIDHOUSING

PALM_BASE

DISTAL_PHALANX_M

MIDDLE_PHALANX_M

PROXIMAL_PHALANX_M

MASTER_GEAR

THUMB_
DISTAL_PHALANX | DXL | DXL_CABLE_S | IDLER

THUMB_
MIDDLE_PHALANX

MIDDLE_PHALANX

PALM_TOP_CAP
SLAVE_SHAFT

DXL_CABLE_L PWR

PROXIMAL_PHALANX

SLAVE_GEAR

DXL_CABLE_J SW-4

DISTAL_PHALANX

Screws:
S1: Flat Head TRS-M2.2x12, 28pc
S2: Flat Head TRS-M2x8, 4pc
S3: Flat Head TRS-M4x12, 2pc
S4: Rounded/Button Head TRS-M2.5x6 Screw, 1pc S5: Flat Head TRS-M2.5x8, 1pc
S6: Flat Head TRS-M3x12, 1pc
S7: Flat Head TRS-M3x8, 7pc
S8: Flat Head TRS-M2x5, 24pc
S9: Flat Head TRS-M3x10, 8pc
S10: Rounded/Socket Head TRS-M4x10, 6pc S11: Flat Head TRS-M2.5x24, 2pc
Dowel Pins:
P1: 1.5x10 Dowel Pin, 6pc
P2: 1.5x5 Dowel Pin, 2pc
P3: 1.5x5 Dowel Pin, 5pc
Bearings & Hardware:
B1: Bearing 126ZZ, 2pc
B2: Bearing 106ZZ, 1pc
B3: Metal Washer For Flat Head Screw, M3, 1pc B4: IGUS JTM-1630-015 Thrust Bearing, 3pc

EN02 Parts:
- Prepare according to BOM (Found in project folder).
- PROXIMAL_PHALANX contains two parts each and must be printed with CF reinforced material.
- Modify the design of PALM_BASE to fit your mounting interface before printing.
- Solder your preferred power header to PWR board.

## Step 1.1 Idler Preparation:

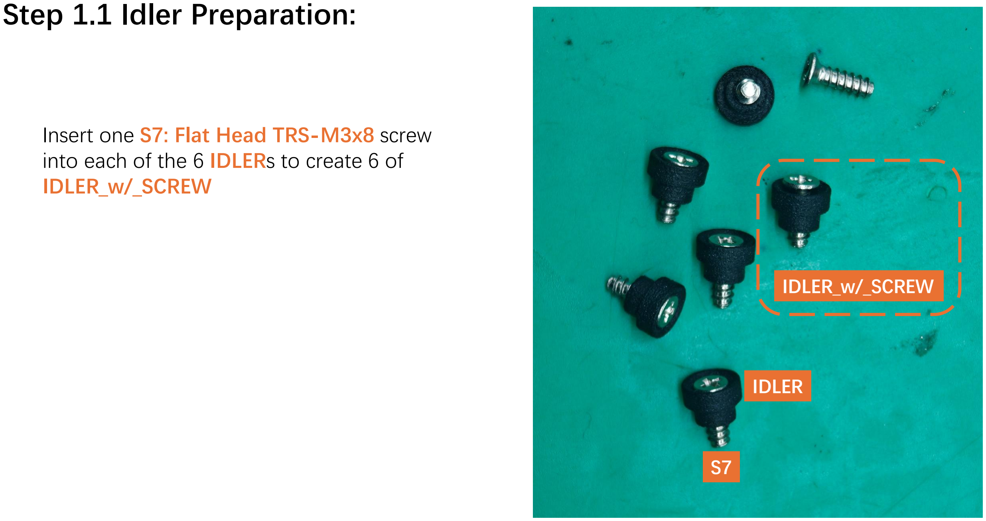
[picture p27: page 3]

Insert one S7: Flat Head TRS-M3x8 screw into each of the 6 IDLERs to create 6 of IDLER_w/_SCREW

S7

IDLER

IDLER_w/_SCREW

## Step 1.2 DXL Preparation:

1. Set the IDs of the 7 Dynamixel XC/XL 330 actuators to 1~7. Note that if you are using six XC-330 and one XL-330 instead of all 7 identical actuators, make sure to set the XL-330 actuator’s ID to 7.
2. Assemble one DXL_CABLE_S cable and one DXL_CABLE_L cable to the XC/XL 330 actuators with ID 1, 3 and 5, on the corresponding ports exactly as shown below.

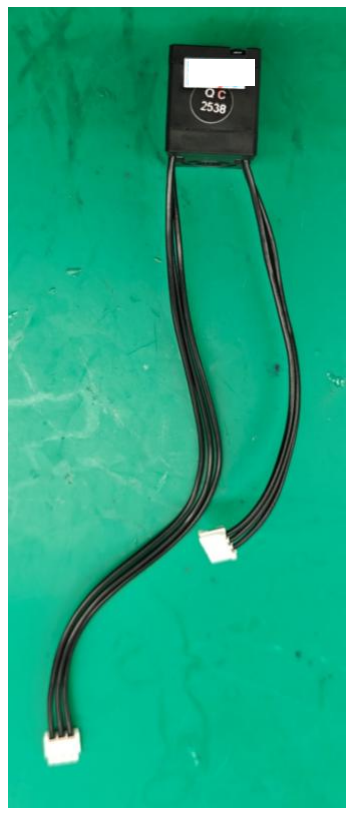
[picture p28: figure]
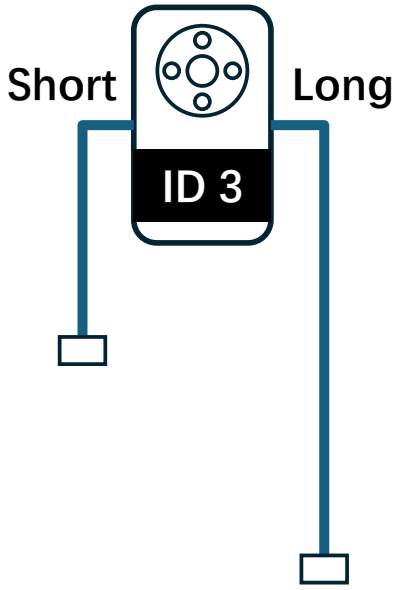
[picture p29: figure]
Short; Long
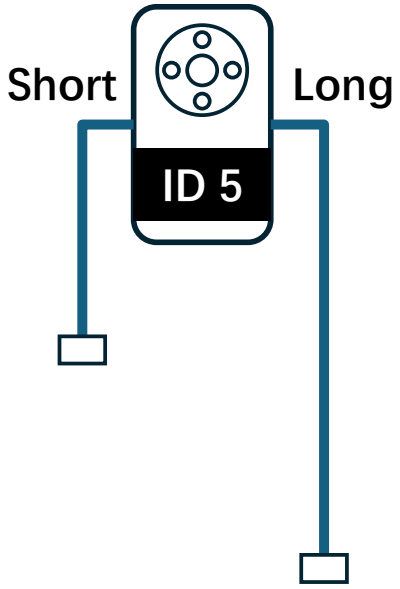
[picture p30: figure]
Short; Long

## Step 2 Index Fingers-1:

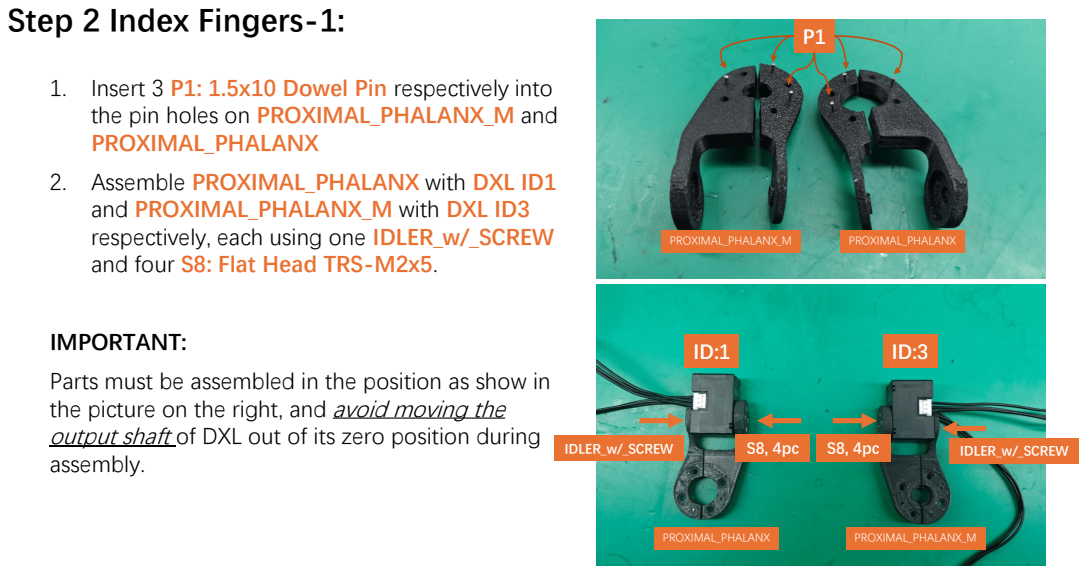
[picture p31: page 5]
PROXIMAL_PHALANX_M; PROXIMAL_PHALANX; IDLER_w/_SCREW

1. Insert 3 P1: 1.5x10 Dowel Pin respectively into
the pin holes on PROXIMAL_PHALANX_M and
PROXIMAL_PHALANX
2. Assemble PROXIMAL_PHALANX with DXL ID1
and PROXIMAL_PHALANX_M with DXL ID3
respectively, each using one IDLER_w/_SCREW
and four S8: Flat Head TRS-M2x5.

IMPORTANT:
Parts must be assembled in the position as show in
the picture on the right, and avoid moving the
output shaft of DXL out of its zero position during
assembly.

## Step 2 Index Fingers-2:

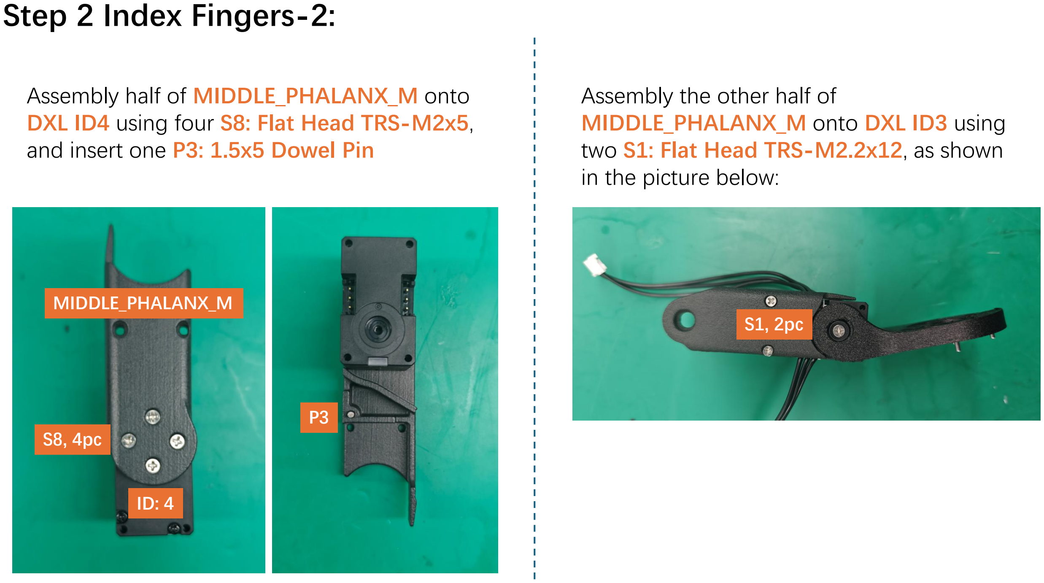
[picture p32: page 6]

Assembly half of MIDDLE_PHALANX_M onto DXL ID4 using four S8: Flat Head TRS-M2x5, and insert one P3: 1.5x5 Dowel Pin

MIDDLE_PHALANX_M

ID: 4

S8, 4pc

P3

Assembly the other half of MIDDLE_PHALANX_M onto DXL ID3 using two S1: Flat Head TRS-M2.2x12, as shown in the picture below:

S1, 2pc

## Step 2 Index Fingers-3:

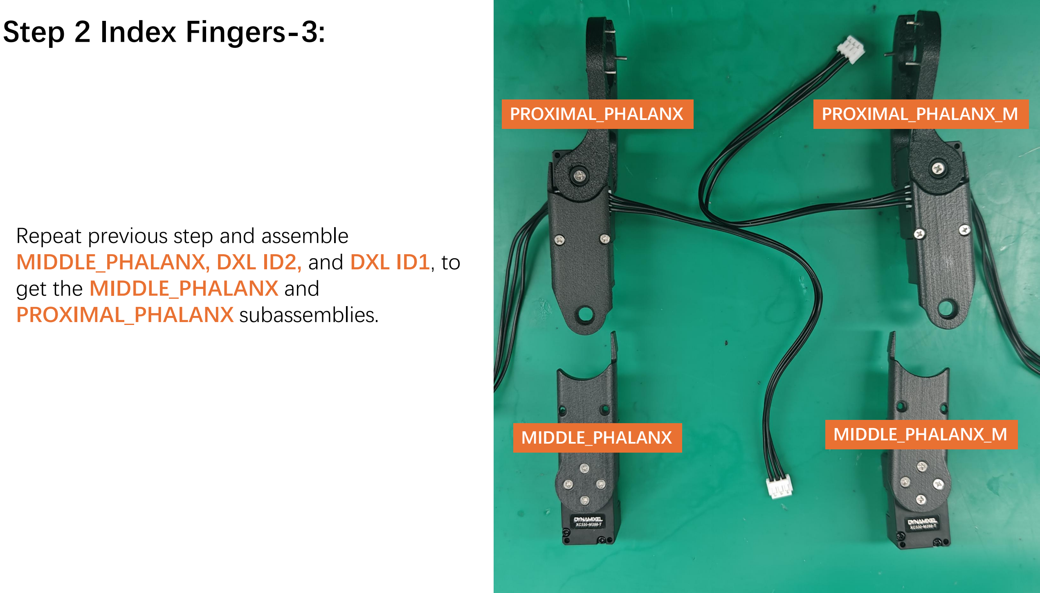
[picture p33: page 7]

Repeat previous step and assemble MIDDLE_PHALANX, DXL ID2, and DXL ID1, to get the MIDDLE_PHALANX and PROXIMAL_PHALANX subassemblies.

PROXIMAL_PHALANX | PROXIMAL_PHALANX_M
MIDDLE_PHALANX | MIDDLE_PHALANX_M

## Step 2 Index Fingers-4:

Route the DXL_CABLE_S connected to DXL ID1 as shown in the picture below, then assemble the MIDDLE_PHALANX subassembly onto the PROXIMAL_PHALANX subassembly and secure with one IDLER_w/_SCREW and two S1: Flat Head TRS-M2.2x12 to form the INDEX subassembly.
Insert the free header of the DXL_CABLE_S cable into the nearby port on DXL ID2.

PROXIMAL_PHALANX

ID: 1

DXL_CABLE_S

PROXIMAL_PHALANX

MIDDLE_PHALANX

INDEX

IDLER_w/_SCREW

S1, 2pc

## Step 2 Index Fingers-5:

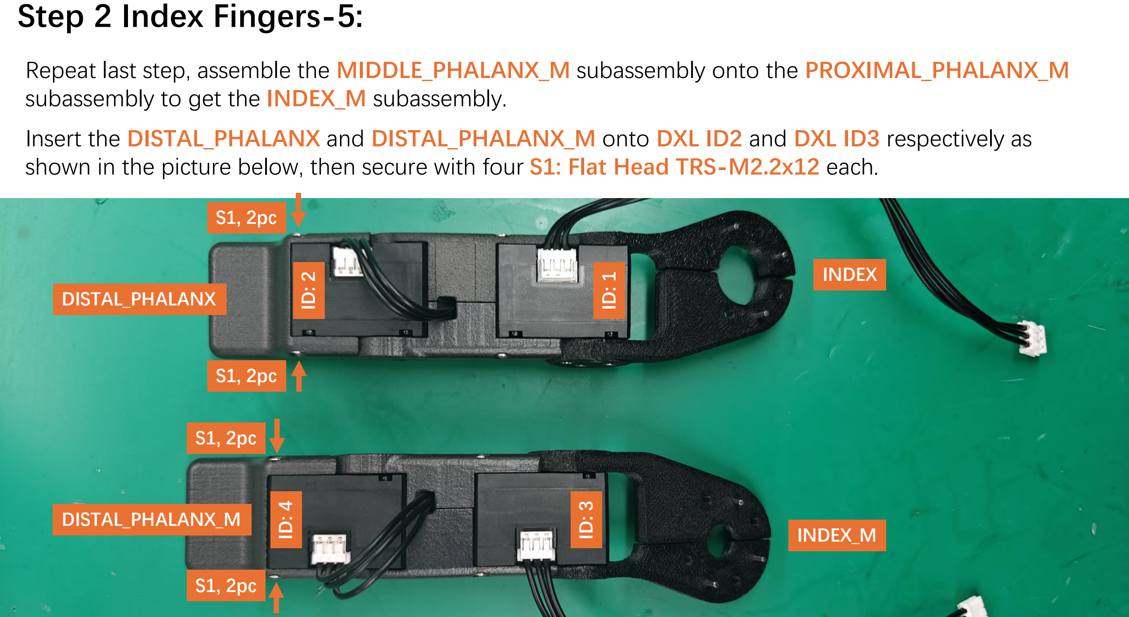
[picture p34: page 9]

Repeat last step, assemble the MIDDLE_PHALANX_M subassembly onto the PROXIMAL_PHALANX_M subassembly to get the INDEX_M subassembly.
Insert the DISTAL_PHALANX and DISTAL_PHALANX_M onto DXL ID2 and DXL ID3 respectively as shown in the picture below, then secure with four S1: Flat Head TRS-M2.2x12 each.

INDEX

INDEX_M

ID: 2

ID: 1

ID: 4

ID: 3
DISTAL_PHALANX_M

DISTAL_PHALANX

S1, 2pc

S1, 2pc

S1, 2pc

S1, 2pc

## Step 2 Index Fingers-6:

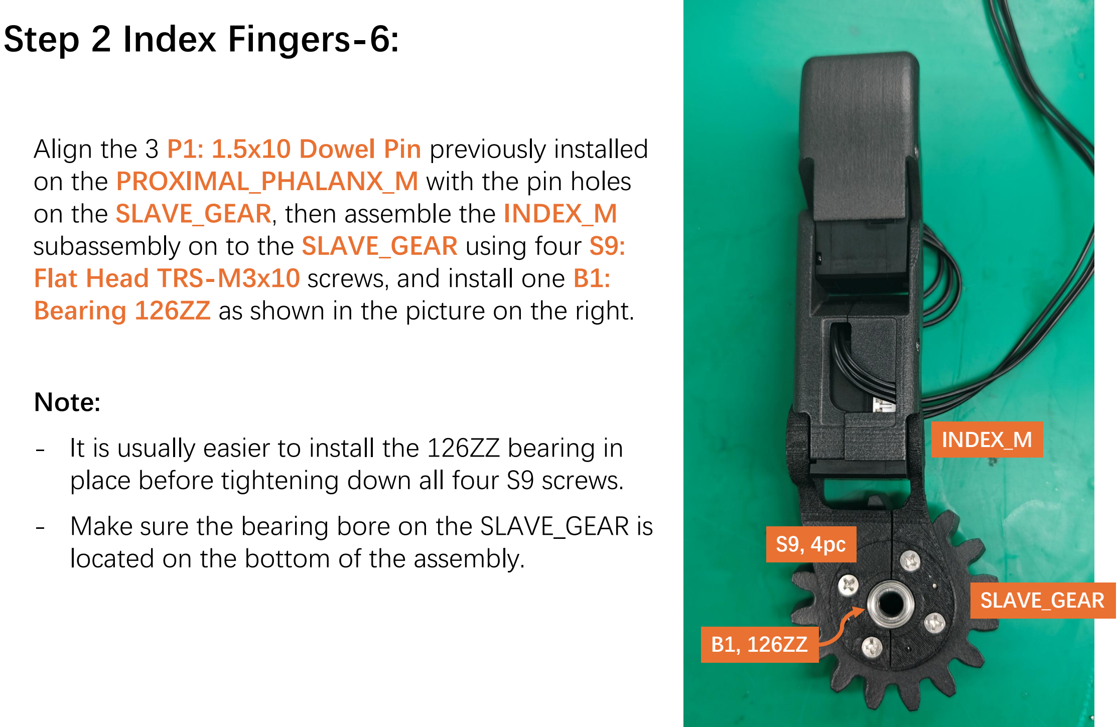
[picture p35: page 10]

INDEX_M

SLAVE_GEAR

S9, 4pc

B1, 126ZZ

Align the 3 P1: 1.5x10 Dowel Pin previously installed on the PROXIMAL_PHALANX_M with the pin holes on the SLAVE_GEAR, then assemble the INDEX_M subassembly on to the SLAVE_GEAR using four S9: Flat Head TRS-M3x10 screws, and install one B1: Bearing 126ZZ as shown in the picture on the right.

Note:
- It is usually easier to install the 126ZZ bearing in place before tightening down all four S9 screws.
- Make sure the bearing bore on the SLAVE_GEAR is located on the bottom of the assembly.

## Step 3 Palm-1:

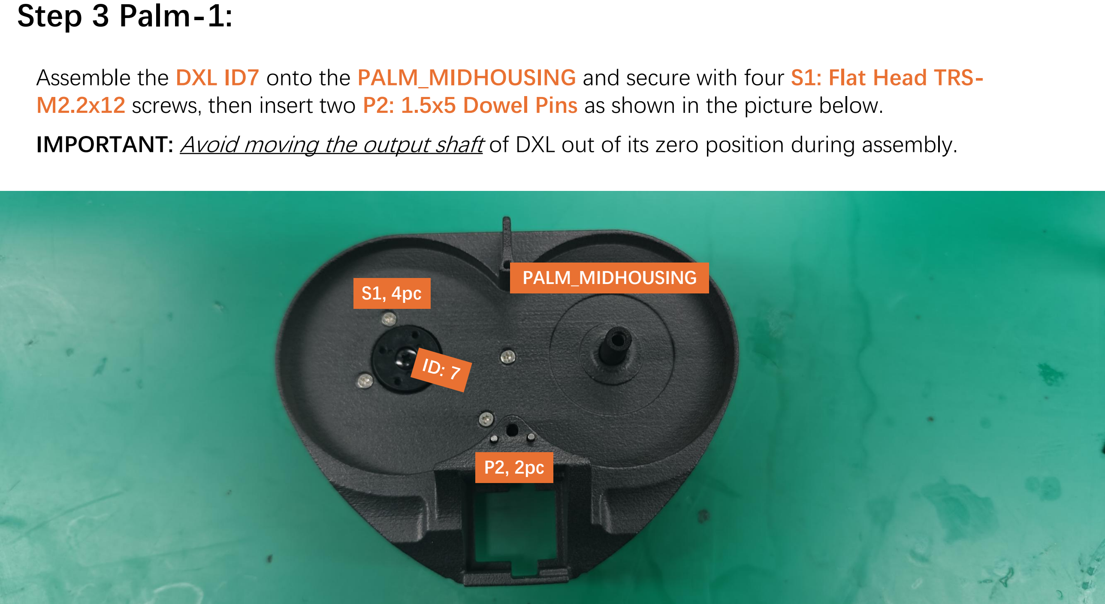
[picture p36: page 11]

Assemble the DXL ID7 onto the PALM_MIDHOUSING and secure with four S1: Flat Head TRS-M2.2x12 screws, then insert two P2: 1.5x5 Dowel Pins as shown in the picture below. IMPORTANT: Avoid moving the output shaft of DXL out of its zero position during assembly.

S1, 4pc

P2, 2pc

PALM_MIDHOUSING

## Step 3 Palm-2:

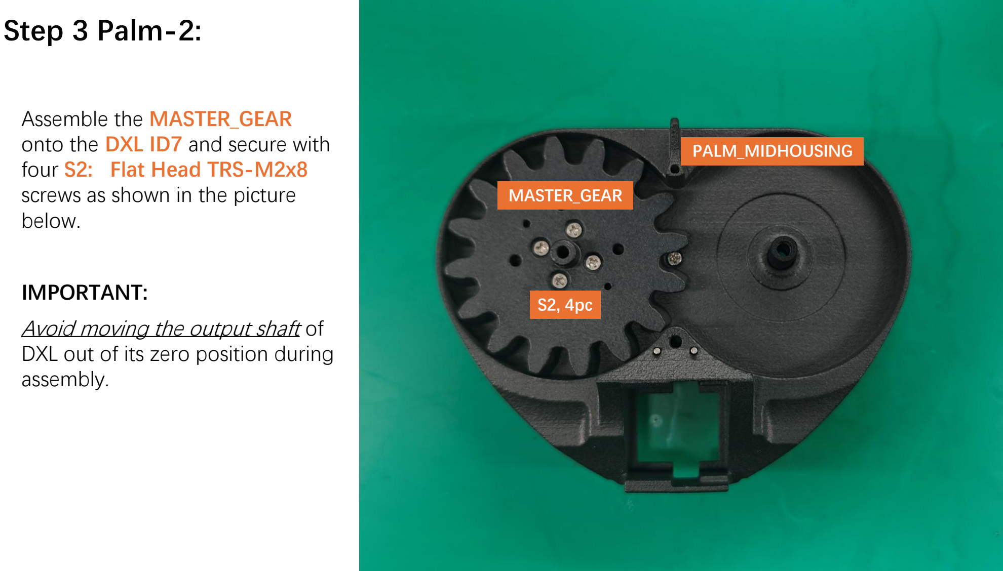
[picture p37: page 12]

Assemble the MASTER_GEAR
onto the DXL ID7 and secure with four S2: Flat Head TRS-M2x8 screws as shown in the picture below.

IMPORTANT:
Avoid moving the output shaft of DXL out of its zero position during assembly.

S2, 4pc

MASTER_GEAR

PALM_MIDHOUSING

## Step 3 Palm-3:

Align the 3 P1: 1.5x10 Dowel Pin previously installed on the PROXIMAL_PHALANX with the pin holes on the MASTER_GEAR, then assemble the INDEX subassembly on to the MASTER_GEAR using four S9: Flat Head TRS-M3x10 screws.

IMPORTANT:
Avoid moving the output shaft of DXL out of its zero position during assembly.

INDEX

MASTER_GEAR

S9, 4pc

## Step 3 Palm-4:

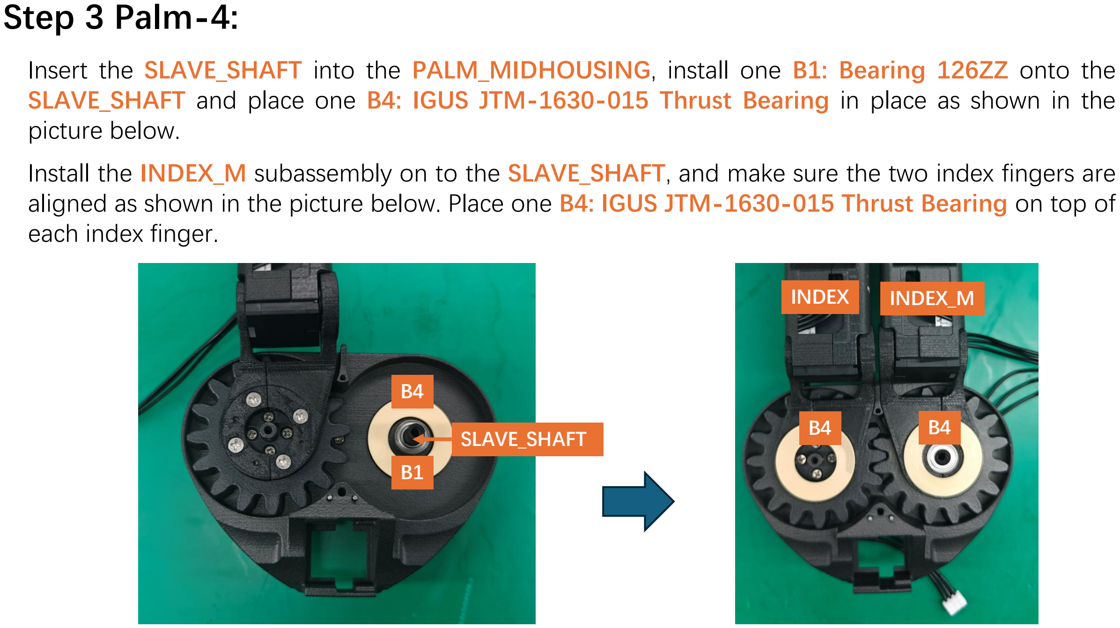
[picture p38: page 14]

Insert the SLAVE_SHAFT into the PALM_MIDHOUSING, install one B1: Bearing 126ZZ onto the SLAVE_SHAFT and place one B4: IGUS JTM-1630-015 Thrust Bearing in place as shown in the picture below.
Install the INDEX_M subassembly on to the SLAVE_SHAFT, and make sure the two index fingers are aligned as shown in the picture below. Place one B4: IGUS JTM-1630-015 Thrust Bearing on top of each index finger.

INDEX INDEX_M

B4

B1

SLAVE_SHAFT | B4 | B4

## Step 3 Palm-5:

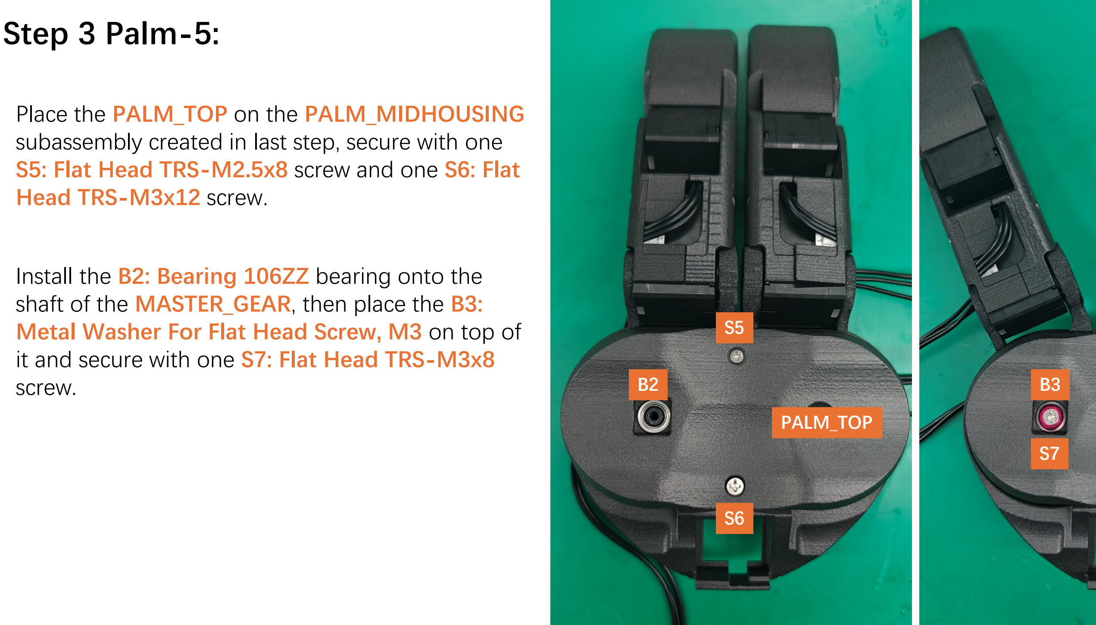
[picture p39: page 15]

Place the PALM_TOP on the PALM_MIDHOUSING subassembly created in last step, secure with one S5: Flat Head TRS-M2.5x8 screw and one S6: Flat Head TRS-M3x12 screw.

Install the B2: Bearing 106ZZ bearing onto the shaft of the MASTER_GEAR, then place the B3: Metal Washer For Flat Head Screw, M3 on top of it and secure with one S7: Flat Head TRS-M3x8 screw.

PALM_TOP

S5

S6

B2 | B3

S7

## Step 3 Palm-6:

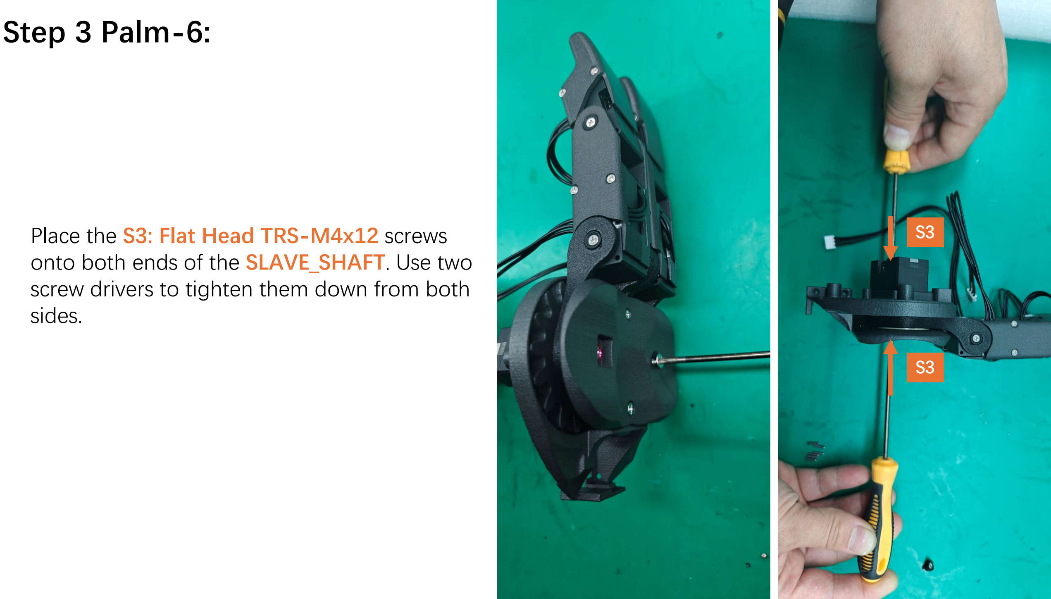
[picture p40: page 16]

Place the S3: Flat Head TRS-M4x12 screws onto both ends of the SLAVE_SHAFT. Use two screw drivers to tighten them down from both sides.

S3

S3

## Step 3 Palm-7:

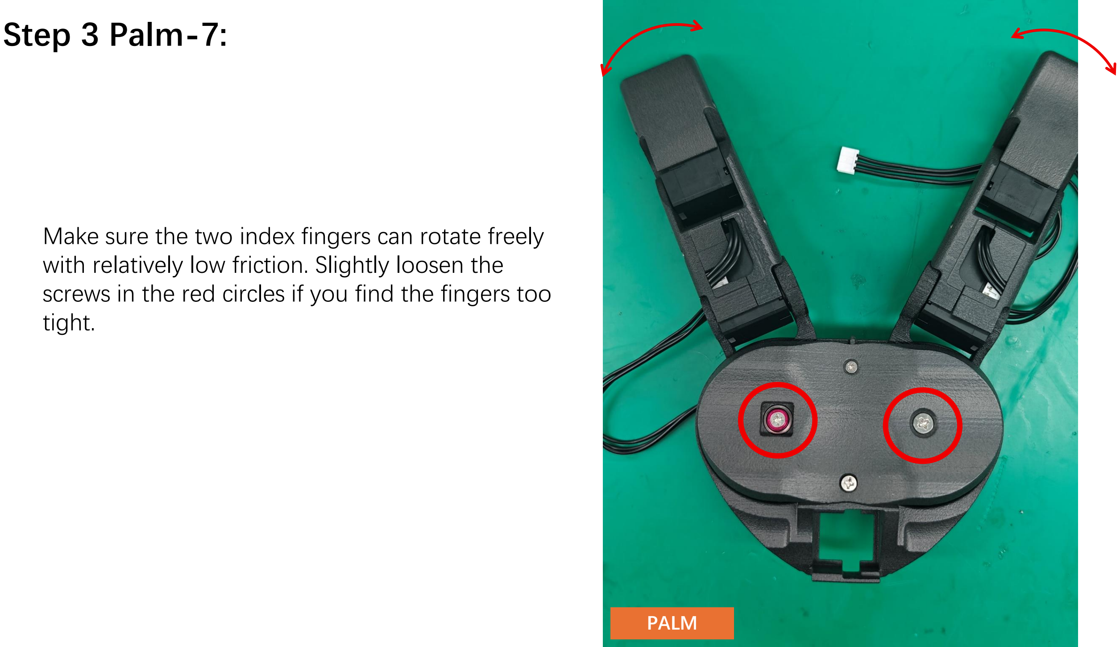
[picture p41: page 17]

Make sure the two index fingers can rotate freely with relatively low friction. Slightly loosen the screws in the red circles if you find the fingers too tight.

PALM

## Step 4 Thumb-1:

Assembly the DXL ID5 and the DXL ID6 onto half of the THUMB_MIDDLE_PHALANX with two S1: Flat Head TRS-M2.2x12 screws and four S8: Flat Head TRS-M2x5 screws as shown in the picture on the right. Insert one P3: 1.5x5 Dowel Pin into the pin hole on THUMB_MIDDLE_PHALANX.
THUMB_MIDDLE_PHALANX

ID: 5

ID: 6

S8, 4pc

P3

S1, 2pc

THUMB

## Step 4 Thumb-2:

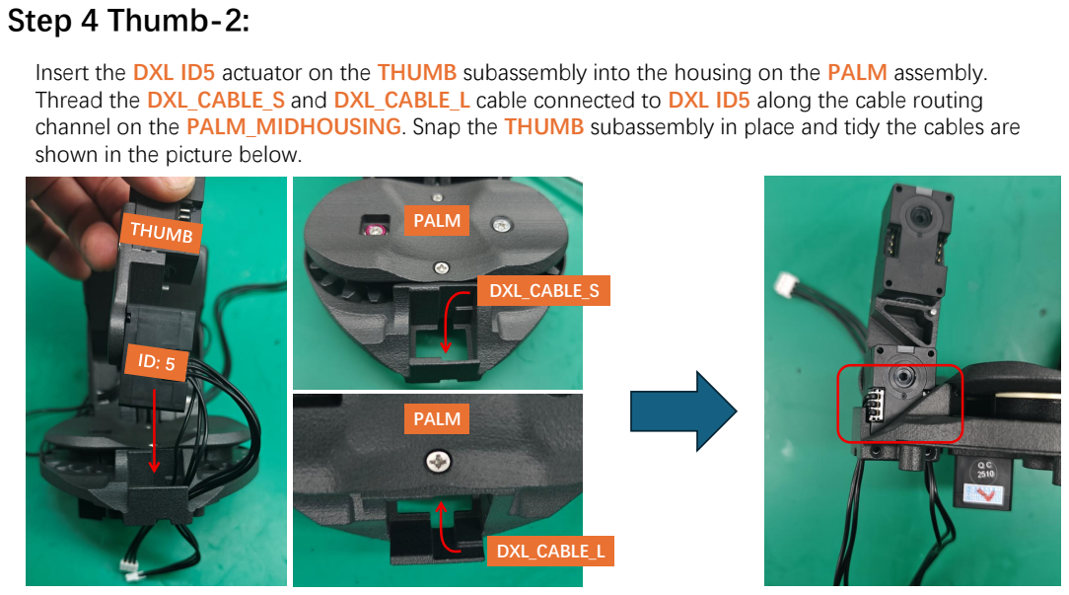
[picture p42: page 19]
DXL_CABLE_L; DXL_CABLE_S; PALM

Insert the DXL ID5 actuator on the THUMB subassembly into the housing on the PALM assembly.
Thread the DXL_CABLE_S and DXL_CABLE_L cable connected to DXL ID5 along the cable routing
channel on the PALM_MIDHOUSING. Snap the THUMB subassembly in place and tidy the cables are
shown in the picture below.

## Step 4 Thumb-3:

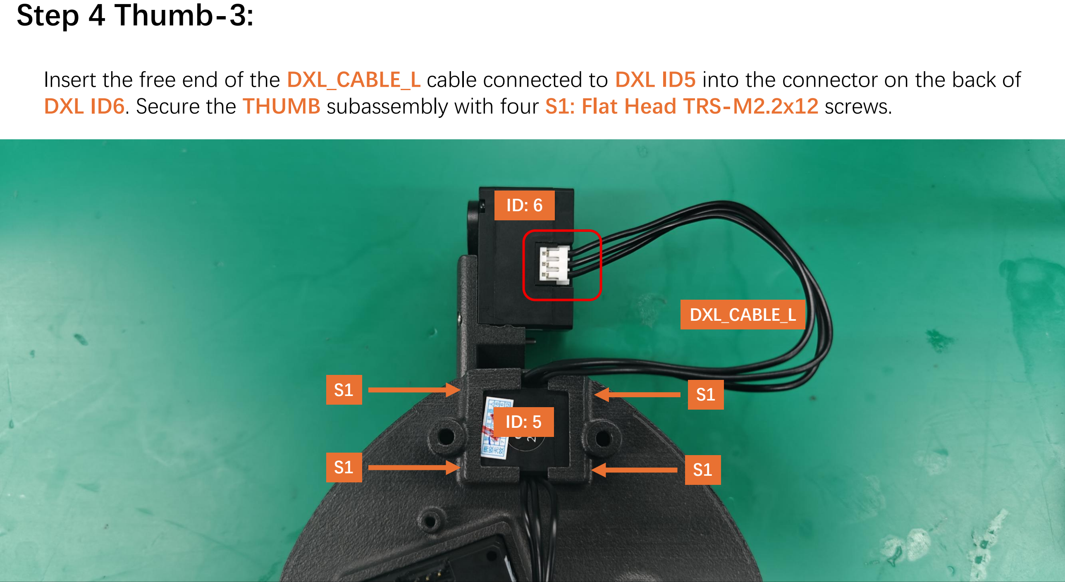
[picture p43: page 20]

ID: 5

ID: 6

DXL_CABLE_L

S1

S1

S1

S1

Insert the free end of the DXL_CABLE_L cable connected to DXL ID5 into the connector on the back of DXL ID6. Secure the THUMB subassembly with four S1: Flat Head TRS-M2.2x12 screws.

## Step 4 Thumb-4:

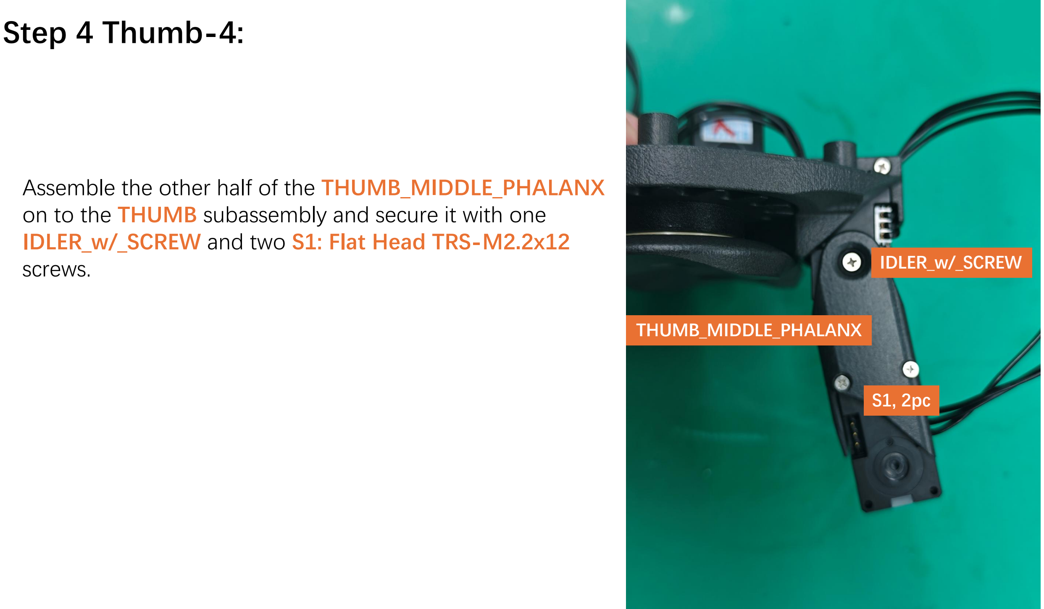
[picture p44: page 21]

THUMB_MIDDLE_PHALANX

Assemble the other half of the THUMB_MIDDLE_PHALANX on to the THUMB subassembly and secure it with one IDLER_w/_SCREW and two S1: Flat Head TRS-M2.2x12 screws.

S1, 2pc

IDLER_w/_SCREW

## Step 4 Thumb-5:

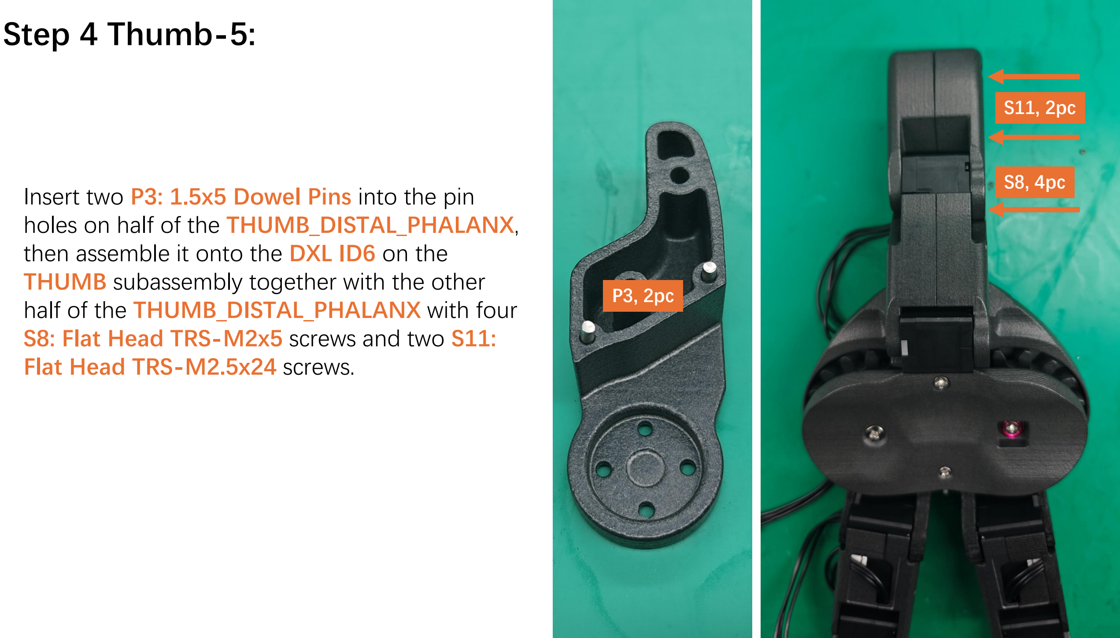
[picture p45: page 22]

Insert two P3: 1.5x5 Dowel Pins into the pin holes on half of the THUMB_DISTAL_PHALANX, then assemble it onto the DXL ID6 on the THUMB subassembly together with the other half of the THUMB_DISTAL_PHALANX with four S8: Flat Head TRS-M2x5 screws and two S11: Flat Head TRS-M2.5x24 screws.

S11, 2pc

S8, 4pc

P3, 2pc

Step 5 Base-1: | DXL_CABLE_L

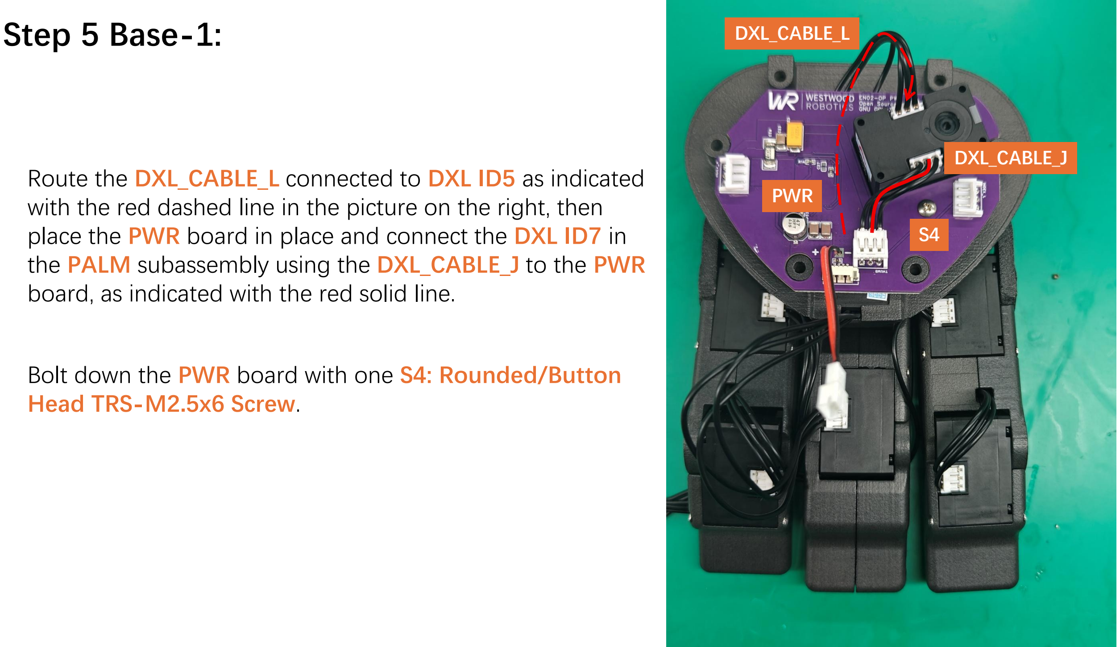
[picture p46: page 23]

DXL_CABLE_J

PWR

Route the DXL_CABLE_L connected to DXL ID5 as indicated with the red dashed line in the picture on the right, then place the PWR board in place and connect the DXL ID7 in the PALM subassembly using the DXL_CABLE_J to the PWR board, as indicated with the red solid line.

Bolt down the PWR board with one S4: Rounded/Button Head TRS-M2.5x6 Screw.

S4

## Step 5 Base-2:

Koala BEAR Muscle Build (example)

PALM_BASE

Customized Mounting Interface

Install your customized PALM_BASE on to the mounting interface on your system before moving on to the next steps. We use a KBMB actuator as an example in the picture below to illustrate the concept.

## Step 5 Base-3:

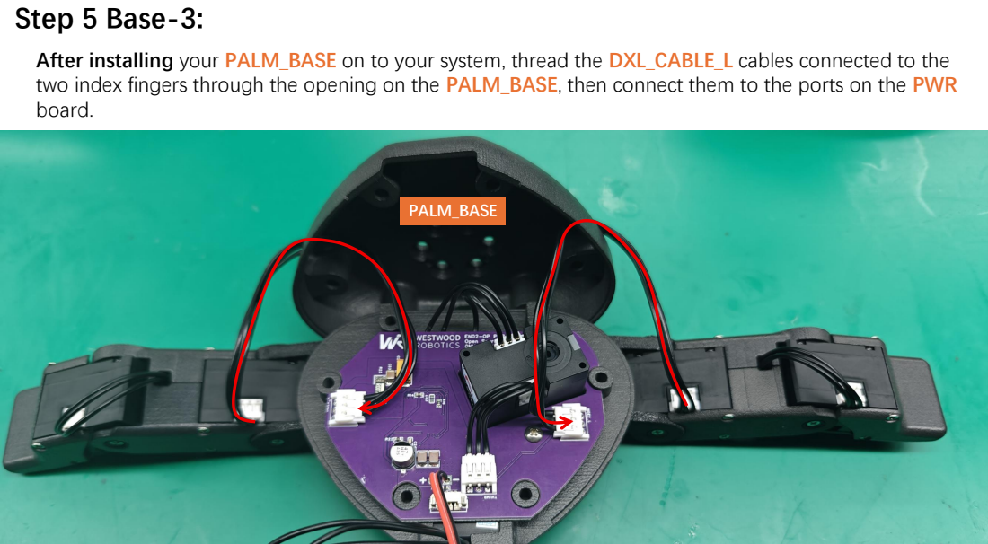
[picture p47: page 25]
PALM_BASE

After installing your PALM_BASE on to your system, thread the DXL_CABLE_L cables connected to the
two index fingers through the opening on the PALM_BASE, then connect them to the ports on the PWR
board.

## Step 5 Base-4:

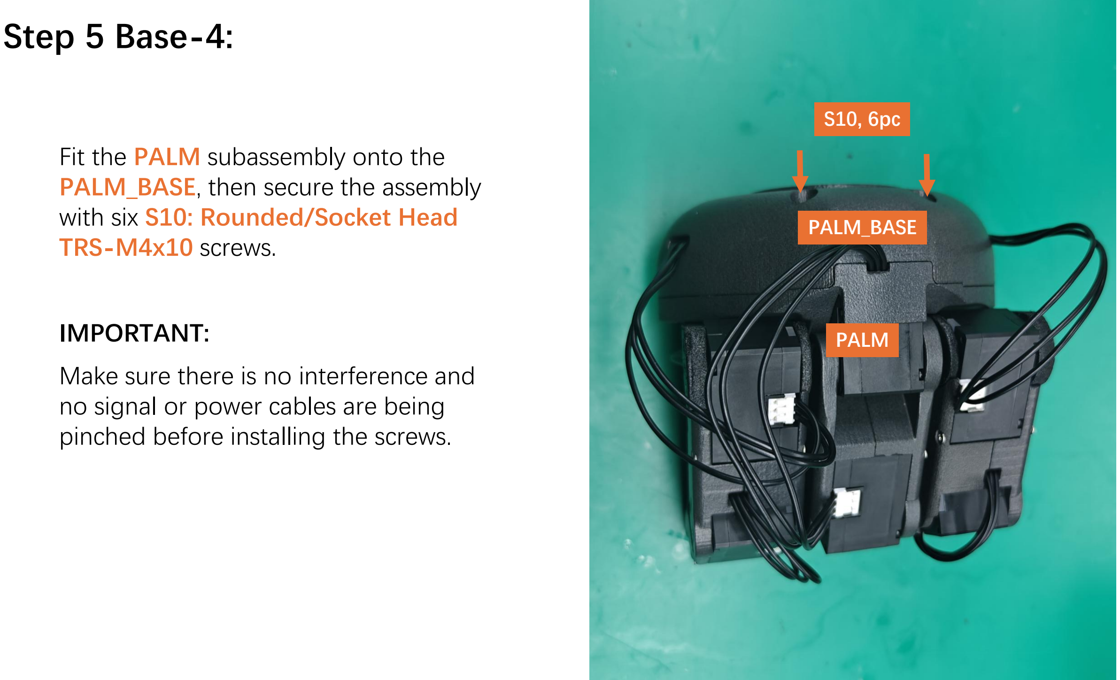
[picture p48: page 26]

Fit the PALM subassembly onto the PALM_BASE, then secure the assembly with six S10: Rounded/Socket Head TRS-M4x10 screws.

IMPORTANT:
Make sure there is no interference and no signal or power cables are being pinched before installing the screws.

PALM_BASE

PALM

S10, 6pc

## Step 6 Protection:

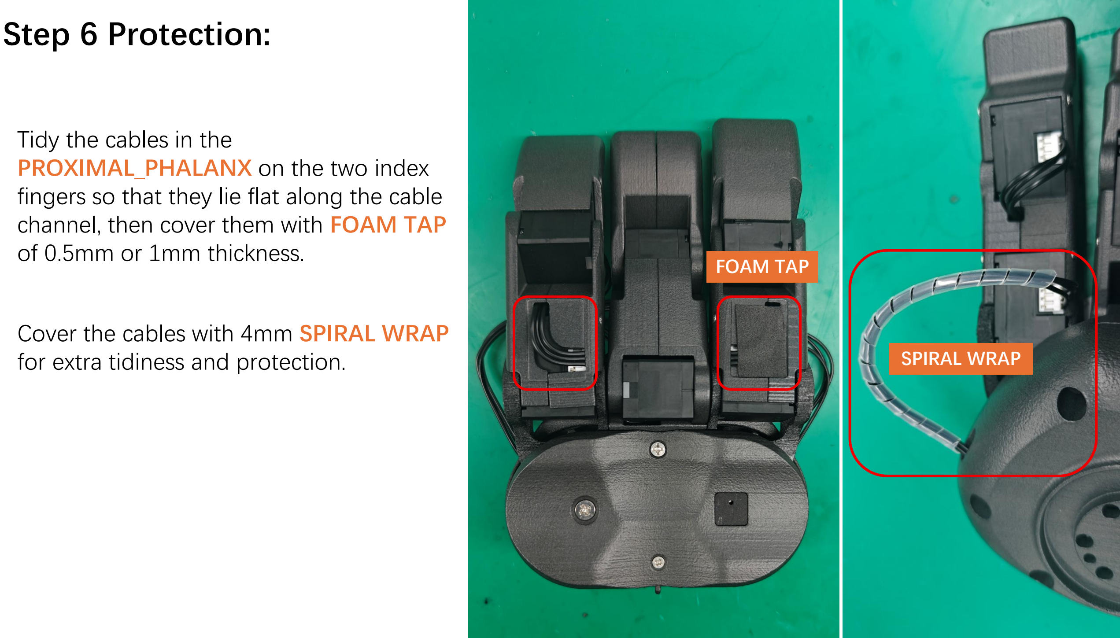
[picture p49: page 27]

Tidy the cables in the
PROXIMAL_PHALANX on the two index fingers so that they lie flat along the cable channel, then cover them with FOAM TAP of 0.5mm or 1mm thickness.

Cover the cables with 4mm SPIRAL WRAP for extra tidiness and protection.

FOAM TAP

SPIRAL WRAP

## EN02-OP Gesture and Application Examples

# THANK YOU & ENJOY!

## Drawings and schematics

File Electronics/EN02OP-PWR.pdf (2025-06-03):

5V 10A

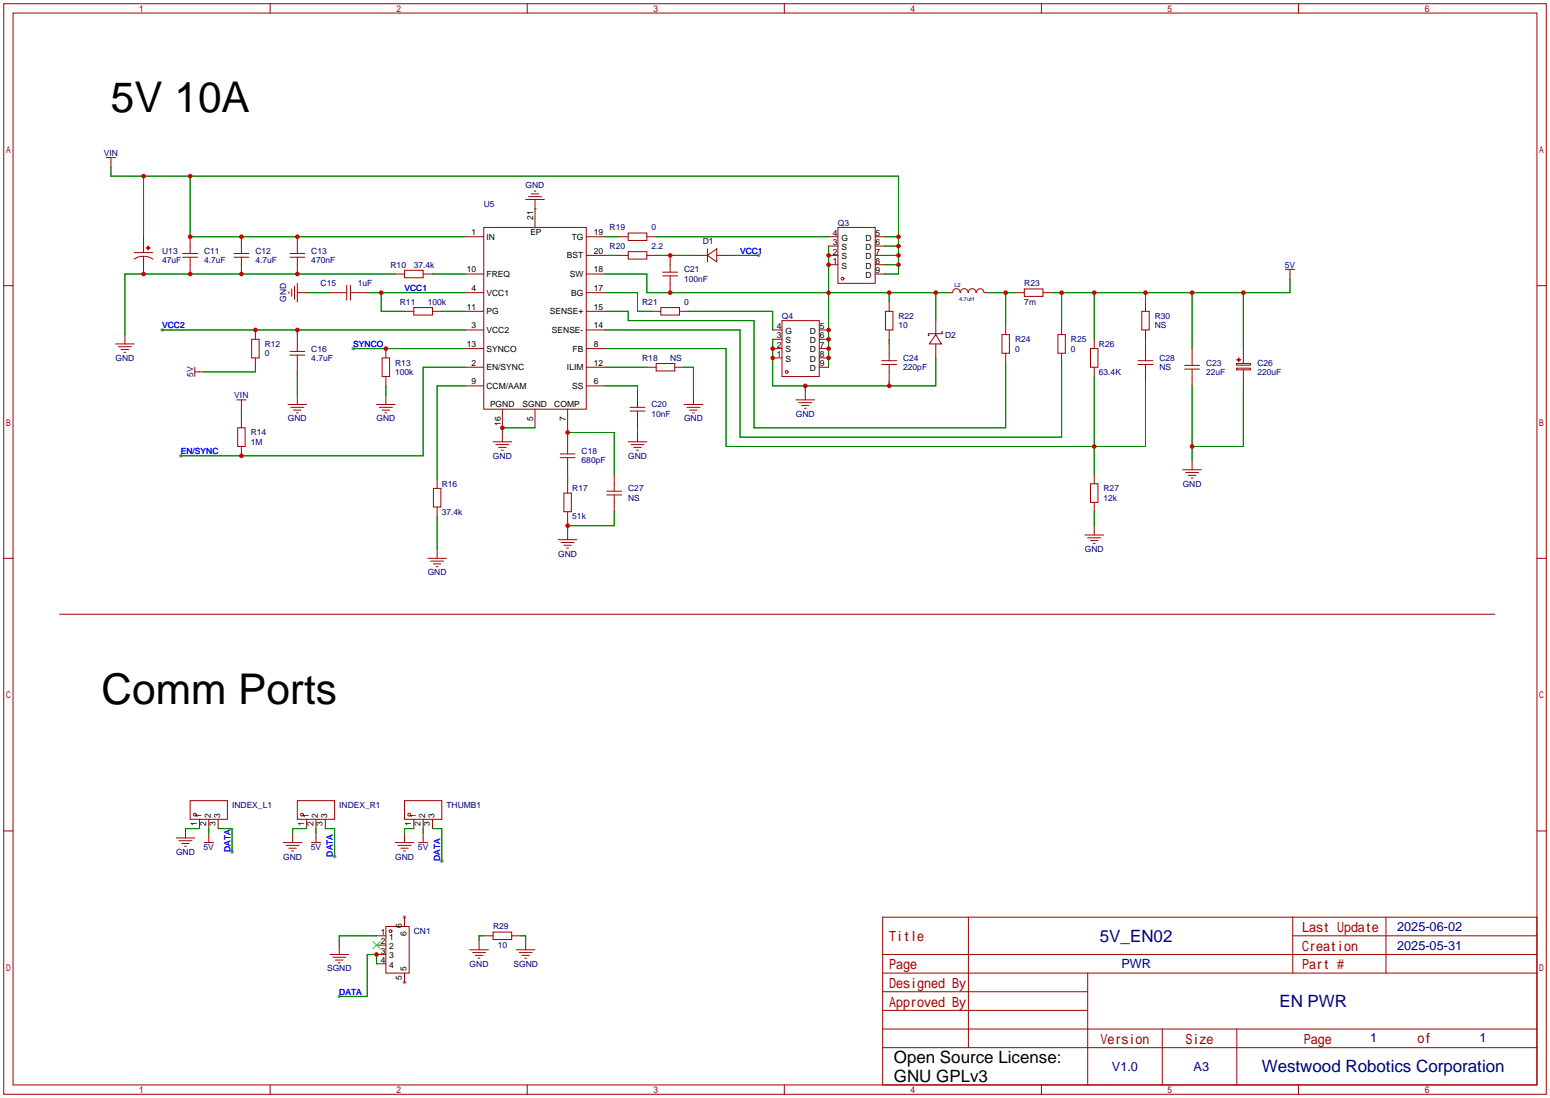
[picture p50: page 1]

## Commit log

2025-06-03 Initial commit with files.
    [EN02-DISTAL_PHALANX-M.STEP, EN02-DISTAL_PHALANX.STEP, EN02-MIDDLE_PHALANX.STEP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]
2025-10-16 Add photos; Update BOM to support 12V systems; Update README.
    [EN02OP-PWR-BOM.xlsx]
2025-11-16 Assembly Guide and Design optimization.
    - The PROXIMAL_PHALANX parts are split into two parts for easier assembly.
    - Fix a problem in previous file that the PALM_TOP_CAP was not separated from the PALM_TOP.
    - Include the Assembly Guide.
    [EN02-OP-BOM.xls, EN02-PALM_TOP.STEP, EN02-PALM_TOP_CAP.STEP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]

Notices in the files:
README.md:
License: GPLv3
